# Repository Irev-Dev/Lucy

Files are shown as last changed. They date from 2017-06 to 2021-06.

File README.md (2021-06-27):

### Notice
Not maintained! Here's the back story. I started this project as way to mix a currenty hobby of racing quads and my new found love of OpenSCAD. As part of developing it I ran into frustrations with not being able to easly add fillets in OpenSCAD and so developed the [Round-Anything](https://github.com/Irev-Dev/Round-Anything) library to support this project. Some life events resulted in putting the project down and it lost steam.

My original [landing page](https://lucy-quad.kurthutten.com/) for lucy is still up in a graveyard state. and the [teaser video can be found here](https://vimeo.com/238244710).

# Lucy
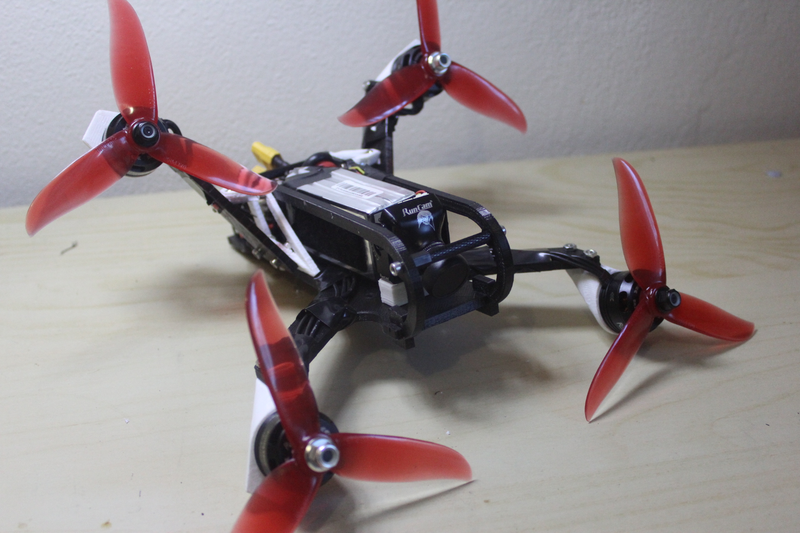
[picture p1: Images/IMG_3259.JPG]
 

OpenSCAD/Parametric Miniquad Frame, designed with aggressively tilted body and with flat arms for minimal blockage of the thrust columns. The result is a quad that is most aerodynamic when flown at its most aggressive angle as opposed to most miniquad frames which become less aerodynamic the further forward they are tilted.

The frame is intended to be made from carbonfiber with some printed parts. It's currently being prototyped so contributions are welcome. The frame also has a [thingiverse](https://www.thingiverse.com/thing:2403189) page, though I prefer to colaborate on github.

## Contributing
I thought it was about time I got this code up on github, so I don't have any immediate ideas of ways to contribute. I need to do an initial tidy of the code and then maybe I'll put together a plan of improvements/features that can be done. But by all means contact me with ideas or make a change and make a pull request.

At this stage the frame has not been tested at all, I have quad components arriving soon, I plan on testing it by printing it completely out of PLA (because it's cheap). It will break the first time it's crashed without a doubt, but I think PLA should be rigid and strong enough while in flight. If the frame progresses nicely and I get some carbonfiber cut I'm not sure what filament should be used for the final printed parts. I have some taulman 910 nylon which I think is probably a good mix of tough and rigid, but perhaps PETG or TPU should be used?

## Features
### Parametric
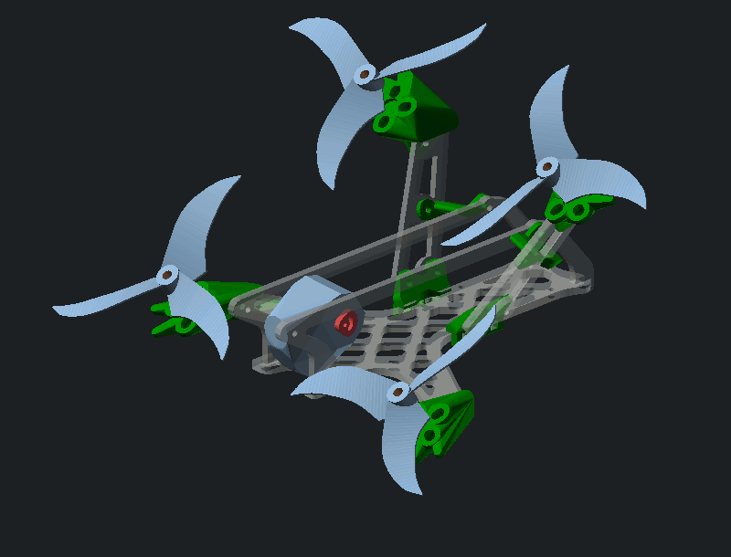
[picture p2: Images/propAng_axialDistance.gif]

Most dimensions can be tweaked. The image above for example shows the angle of the body relative to the props varying from 40 to 70 degrees and the distance between the rear props changing from 180 to 130mm.

### Low Drag
This is where I hope this frame will come into it's own. Most quad frames have a elongated body which creates negative lift while flying and creates more drag the more aggressively the quad is flown, while compact frames reduce this somewhat the arms of the quad still block a large amount of the thrust column which is inevitable when the motors are mounted directly to carbon fiber sheet. Lucy Kwad gets around this by having a very aggressively tilted body and tilted motor mounts. The body is tilted further than the camera angle so that during medium speed flight there is some drag but also some positive lift and in top speed flight the frame will be tilt so as to have the least drag. The arms of the quad are tilted at the same angle as the body thanks to the tilted motor mounts.
The image below shows the body tilt at a greater angle than the camera. 70 degrees in the images though this is a guess, testing is needed.

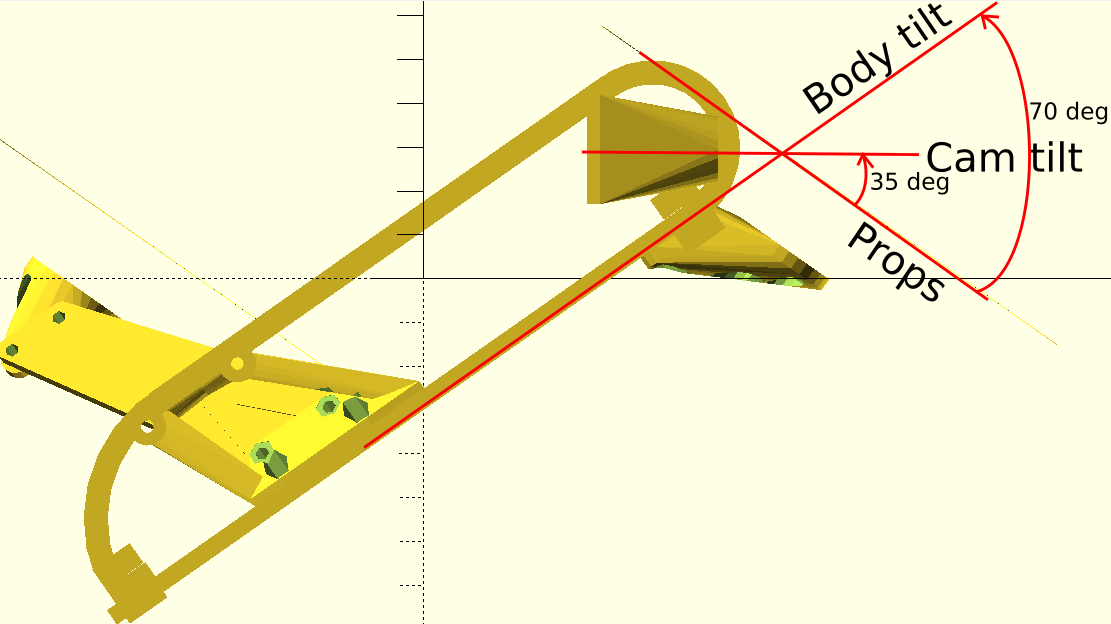
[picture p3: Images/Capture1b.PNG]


## Updates

26/06/2017 - Inital commit

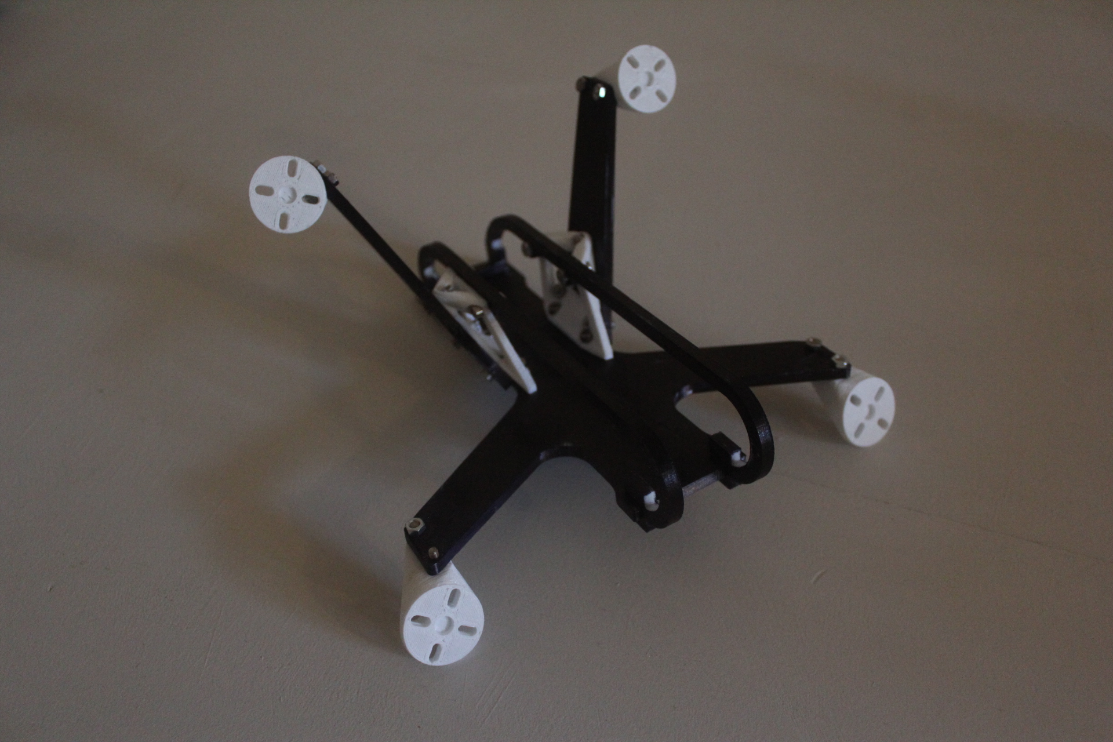
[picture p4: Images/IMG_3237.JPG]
 

28/06/2017 - I have spent the last two nights getting the code ready enough to print for the first (what I hope will be) flyable version. I got motivated when my motors arrived. I will print it out of PLA, it won't last long but hopefully I get an idea of how it will fly. 

30/06/2017 - I have done about 70% of the build for the first prototype. I'm getting excited. I had to put the props on just to see what it looks like, pretty happy with the aesthetics :)
The PLA is definitely worrisome. Because of the design of the quad the arms are still rigid enough in the direction of thrust bit I'm worried about the torque of the motors during fast spool ups. If it expodes when I punch it I just hope it doesn't damage any of the electronics. 

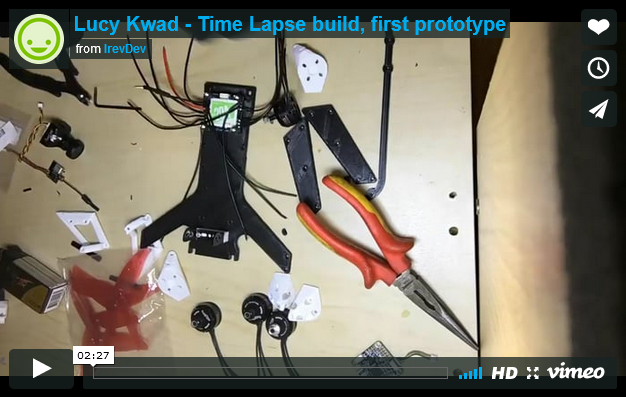
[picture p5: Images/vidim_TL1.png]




11/08/2017 - Got back to working on this and finish the electronics for the first prototype, ran into some interesting problems. With the default PID's as soon the quad armed it would start vibrating and would generate enough lift form trying to correct itself that it would start to take off. halving the PID values didn't fix it, and neither did quartering them. Then I tried re-enforcing the arms quickly with some balsa wood (as shown below) and now it seems to fly well with halved default PID values. This is the problem with using PLA, I won't be able to tune it properly and therefore see how it will actually fly until I bite the bullet and get it made in carbon fiber. It's been interesting trying to get it to fly though.

I have only done line of sight hovering so far, I hope to take it for a good FPV flight soon.

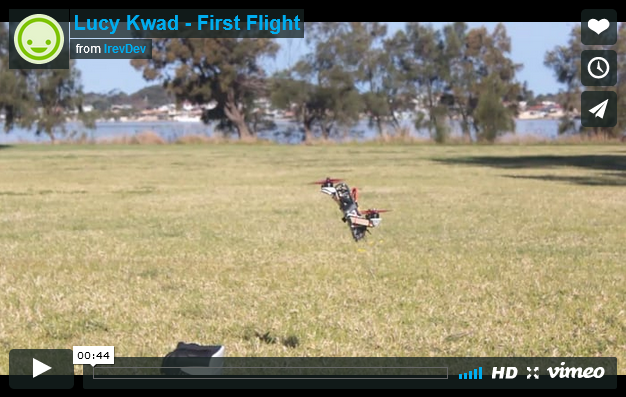
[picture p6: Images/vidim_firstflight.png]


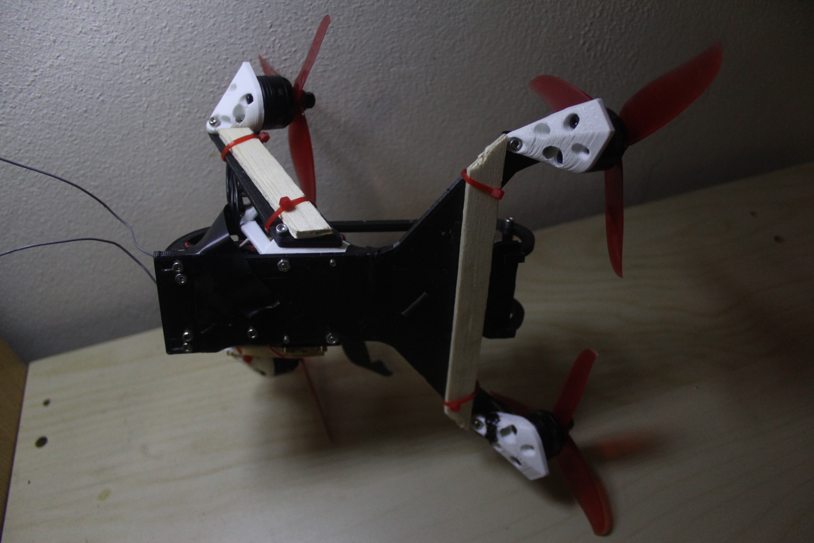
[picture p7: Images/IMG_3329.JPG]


15/08/2017 - A large update to the Lucy code just got merged into the master project on github. The change centers around the heavy use of the [polyRound()](https://github.com/Irev-Dev/Round-Anything) function instead of relying on primitives so much. Snap shot of the work in progress below.

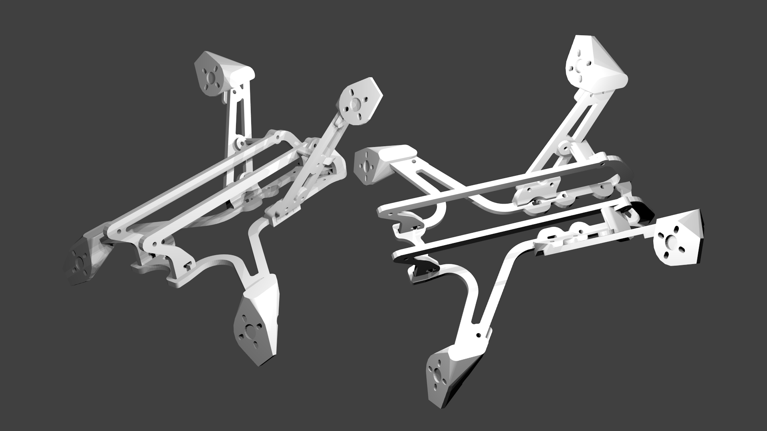
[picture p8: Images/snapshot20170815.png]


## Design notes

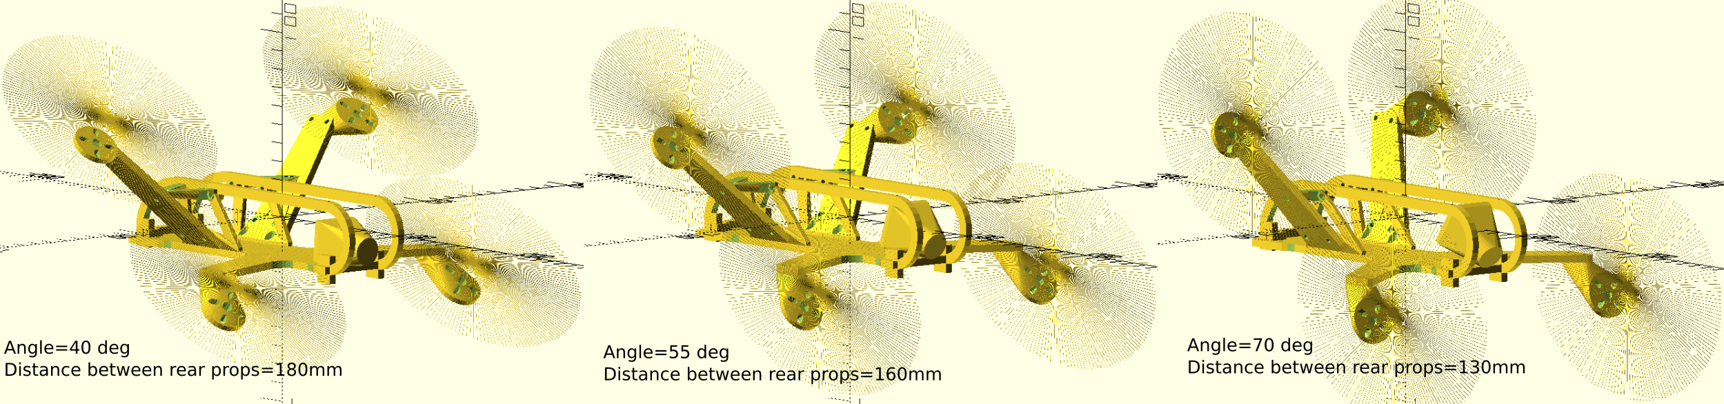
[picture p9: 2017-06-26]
Images/Capture11.png

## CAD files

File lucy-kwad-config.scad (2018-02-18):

/* 
Intellectual property is bullshit, steal this code

This code is licensed under GLPv3, which gives you permission to edit this code to meet your own purposes. 
However the idea that you need permission to edit and hack the things around you is insidious, 
and has been promoted by those who do not have your interests in mind. 
Intellectual property is bullshit.
*/

//include the modules 
include <lucy-kwad-modules.scad>
//include polyround tool 
include <libraries/polyround/polyround.scad>


//echo($vpr);echo($vpt);echo($vpd);//rotation, translation, camdist? focal?
//$vpr=[69.7, 0, 51.6];$vpt= [-1.03859, 2.44642, 3.51505];$vpd=412;//comment to stop the view from resetting each time

//VARIABLES//
PropD=5*25.4;//propsize inch
$fn=20;
gfn=6;
mot_s = [PropD+8,PropD+40,110,PropD+10]; //[x,yforLowMots,Z,YforUpMots]
dem=max(mot_s[0],mot_s[1],mot_s[3]);

theta = 70;
motP_MT = 3;//material thickness
motP_MT2=3;
motP_mntS=[15.8/2,19.2/2,15.8/2,19.2/2];//mount hole spacing [radA1,radA2,radB1,radB2]
motP_mntD = 3.2;//mounting hole diametr
motP_HD=6.5;//hex diameter
motP_HoS=6;//hex or square (hex=6,square=4);
motP_WMHCS=1.5;//Wing mount hole, counter sink start
motP_dia = 28;
motP_CD=6; //counter dia
motP_CA=45;//counter angle
motP_BR=4;//brace radius
motP_MG=[1,7];//diameter,offset from motP diameter
//motP_WMD=3.2;//wing mount dia
//motP_WMFD=5.7;//fastener dia
//motP_WMFS=6;//fasterner shap (6=hex,4=square)
motP_WMHD=7;//bolt head dia
//motP_WMFDp=2;//fasterner depth
motP_CHD=2;
motP_CHdia=9.5;

//none of these are used, though I might later?
//mot_ht=12;
//mot_dia=22;
//prop_ht=8;
//prop_dia=5*25.4;

//UWB upper wing brace
//UWB_min=3;//minimum material thickness
//UWB_MT=[4,3]; //material thickness1
//UWB_fast=[3.2,5,5.5,3,6];//[dia,head dia,hex dia,hex depth,hexOrSquare]fastner options
//UWB_BMH=4;//BMH
//UpperWingBrace(MT1=UWB_MT1,MT2=UWB_MT2,Hdia=UWB_Hdia,WBMO=UWB_MO)
UWB_MT1=2;
UWB_MT2=3;
UWB_Hdia=3.2;
UWB_MO=[5,4];//[x,z]
//this will be used soon
UWB_minP=0.5;//min print thickness (support material)
UWB_HoS=6; //hex or square 4=square 6=hex

//fuselage and rails, FR=fuselage rails
fs=[185,30+9,43]; //length width height
fs_mir=1;//min internal radius (set by the size of your routing bit)
fs_mer=0.2;//min external radius
fs_sr=2;//standard radius
fs_wtr=2;//wing tip radius
fs_wbr=[12,20];//wing base radius, [front, rear]
fs_minT=4;//min thickness
fs_bhd=5.7;//bolt head dia
fs_bd=3.2;//bolt dia
fs_bhh=3;//bolt head height
fs_bmt=3;//bolt min thickness
fs_ph=4;//post height
fs_pt=4;//post thickness
fusehozoff=-20;
FR=[4,5,6,65,35]; //[carbon thickness,other thickness,trasition radius, front angle, rear angle]
CarRT=4;
CarBT=FR[0];
RCutT=5.5;

//frameRail
FR_SD=[5,5];//slot depth1,slot depth2
FR_tol=0.2;
FR_CaT=4;//carbon thickness
FR_CuT=7;//cut thickness
FR_MT=3;//min thickness
FR_RA=20;//rear angle
FR_OH=13;//front overhang
FR_MIR=1;//min internal radius
FR_SR=3;//standard radius
FR_R1=20;//radius 1
FR_R2=5;//radius 2
FR_R3=10;//radius 3
FR_BHD=7;//bolt head dia
FR_BD=3.2;//bolt dia
FR_BHH=3;//bolt head height

WB_RSD=5;//rail slot depth
WB_CaT=4;
WB_PW=4;//post width
WB_mir=1;
WB_XP=-56;//X position
WB_BNO=1.5;//bottom nut offset
WB_tol=0.2;

Stack_HS=30.5;
Stack_HD=3.2;
Stack_PcbW=38;

//rough model of runcam eagle
camL=33; //length
camH=26.5; // height
camW=27;//width
camD=17;//lens diameter
camPP=3;//pivit point
camA=[theta,10];//angle
camMH=25;//mount height
camP=[fs[0]/2-43,24];//placement, [X,Z]
camRR=18;//rear room (behind camera)
camHP=[2,7];
camST=0.55;//shell thickness
camMT=2;//min thickness
camBMD=3.2;//bottom mount diameter
camBMH=12;//bottom mount height

//rearfastening
rearF_nh=2.5;// nut height
rearF_nf=5.3;// nut flats (distance between flats)
rearF_ha=20;//hull angle
rearF_bd=3.2;//bolt diameter

//CALCULATIONS// and some varibles

mot_cords=[[(mot_s[0]*cos(theta)+mot_s[2]*sin(theta))/2,mot_s[1]/2,(-mot_s[0]*sin(theta)+mot_s[2]*cos(theta))/2],
[(-mot_s[0]*cos(theta)-mot_s[2]*sin(theta))/2,mot_s[3]/2,(mot_s[0]*sin(theta)-mot_s[2]*cos(theta))/2]];
carbW=[33,23,4,4]; //wing [base width, tip width, thickness,radius]
carbWmin=2; //wing min thickness
carbLWTO = [-5,-3,15]; //lower wing tip offset [x,y,z]
carbLWR=[10,20];//lower wing radius [front,rear]
carbLWP=[22,fs[1]/2,mot_cords[0][2]+carbLWTO[2]]; //lower wing placement [x,y,z]
carbUWP=[-28,(fs[1]+carbW[2]*0)/2,carbLWP[2]+CarBT/2+UWB_MO[1]*0]; //lower wing placement [x,y,z]
carbUWTO = [-5,-12,-5]; //lower wing tip offset [x,y,z]
FR_RHP=[-fs[0]/2+fusehozoff+FR_SD[0]-FR_CuT+fs[2]*tan(FR_RA)+11,fs[2]-FR_CuT/2];//Rear hole placement, todo hardnum curently offset from the corrner of the rail by an abitary amount, ideally the hole should be placed just behind the wing so that it is still accessible with a allan key

LWXang = atan((mot_cords[0][2]+carbLWTO[2]-carbLWP[2])/(mot_cords[0][1]+carbLWTO[1]-carbLWP[1]));
UWXang = atan((mot_cords[1][2]+carbUWTO[2]-carbUWP[2])/(mot_cords[1][1]+carbUWTO[1]-carbUWP[1]));

TeMT=3;//tether Min thickness

//Upper wing Y length
UWYlen=pointDist([carbUWP[1],carbUWP[2]],[mot_cords[1][1]+carbUWTO[1],mot_cords[1][2]+carbUWTO[2]]);
//Upper wing radii points

UW_FWO=3; //front wing offset
UWingRP=[
[carbUWP[0],							UW_FWO,		3],
[mot_cords[1][0]+carbUWTO[0],			UWYlen,		3],	
[mot_cords[1][0]+carbUWTO[0]-carbW[1],	UWYlen,		3],	
[carbUWP[0]-carbW[0],					0,			3],
[carbUWP[0]-carbW.x/2,					UW_FWO,		10]
];
UWRYang=getAngle(UWingRP[2],UWingRP[3]);
UWFYang=getAngle(UWingRP[1],UWingRP[0]);

UWing_MFBMY=UWingRP[1].y-14;//motor front bottom mount Y
UWing_MRBMY=UWingRP[2].y-5;//motor rear bottom mount Y
UWing_MFBMSY=UWingRP[1].y-5;//motor front bottom mount small Y
UWing_MFBMX=interpX([UWingRP[0].x,UWingRP[0].y],[UWingRP[1].x,UWingRP[1].y],UWing_MFBMY);//motor front bottom mount X
UWing_MRBMX=interpX([UWingRP[3].x,UWingRP[3].y],[UWingRP[2].x,UWingRP[2].y],UWing_MRBMY);//motor rear bottom mount X
UWing_MFBMSX=interpX([UWingRP[0].x,UWingRP[0].y],[UWingRP[1].x,UWingRP[1].y],UWing_MFBMSY);//motor front bottom mount small X
UWing_XMHO=-carbWmin*3/cos(90-getAngle(UWingRP[0],UWingRP[1]));//X mount hole offset

UWing_BTO=11;
//UWing_MMH=round3points([UWing_MMP(4),[UWing_MMP(1)[0],UWing_MMP(1)[1],motP_mntD/2],UWing_MMP(2)])[2]+[UWing_XMHO,0];//motor mount hole
UWing_MMH=round3points([UWing_MMP(3),[UWing_MMP(0)[0],UWing_MMP(0)[1],(motP_mntD+motP_MT)/2],UWing_MMP(1)])[2]+[UWing_XMHO*0,0];//motor mount hole
UWing_FWMH=round3points([UWingRP[3],[UWingRP[0].x,UWingRP[0].y,5],UWingRP[1]])[2];//front wing mount hole
UWing_RWMH=round3points([UWingRP[2],[UWingRP[3].x,UWingRP[3].y,5],UWingRP[0]])[2];//rear wing mount hole
UWing_TMHY=(fs[2]/*-(carbUWP[2]-carbLWP[2])*/-UWB_MO[1]-FR_CuT)/sin(UWXang)-10;//Tether Mount Hole Y
//UWing_TMHY=(+fs[2]+carbUWP[2]-FR_CuT/2)/cos(UWXang);//Tether Mount Hole Y
TePoint=[100,fs.y/2,(carbLWP.z+fs.z/*-(carbUWP[2]-carbLWP[2])*/-FR_CuT*1.5)];//tether point - bad name will do for now.
//TePoint2=[100,carbUWP.y+(fs[2]/*-(carbUWP[2]-carbLWP[2])*/-UWB_MO[1]-FR_CuT)*cos(UWXang)+(carbW[2]/2+TeMT)*cos(UWXang)+TeMT*sin(UWXang),(carbLWP.z+fs.z/*-(carbUWP[2]-carbLWP[2])*/-FR_CuT*1.5-FR_CuT*cos(UWXang))];//tether point - bad name will do for now.
TePoint2=[-0,carbUWP.y,carbUWP.z]+[0,(UWing_TMHY-FR_CuT/sin(UWXang))*cos(UWXang)+(carbW[2]/2+TeMT)/sin(UWXang),(UWing_TMHY-FR_CuT/sin(UWXang))*sin(UWXang)];//(fs[2]-UWB_MO[1]-FR_CuT)/sin(UWXang)-FR_CuT*0-FR_CuT*sin(UWXang)];//tether point - bad name will do for now.
//#translate(TePoint)sphere(0.2);
//#translate(TePoint2)sphere(0.2);//translate([0,-10,0.2])cube([1,20,1]);
//UWing_TMHY=(fs[2]/*-(carbUWP[2]-carbLWP[2])*/-UWB_MO[1]-FR_CuT)/sin(UWXang);//Tether Mount Hole Y
UWing_TMHX=interpX([UWingRP[3].x,UWingRP[3].y],[UWingRP[2].x,UWingRP[2].y],UWing_TMHY)+9;//Tether Mount Hole X

UWing_BFT=[interpX([UWingRP[0].x,UWingRP[0].y],[UWingRP[1].x,UWingRP[1].y],UWingRP[0].y+UWing_BTO),UWingRP[0].y+UWing_BTO];//brace front top Y
UWing_BRT=[interpX([UWingRP[3].x,UWingRP[3].y],[UWingRP[2].x,UWingRP[2].y],UWingRP[3].y+UWing_BTO),UWingRP[3].y+UWing_BTO];//brace rear top Y
UWing_BFB=[interpX([UWingRP[0].x,UWingRP[0].y],[UWingRP[1].x,UWingRP[1].y],UWingRP[0].y-20),UWingRP[0].y-20];//brace front bottom Y
UWing_BRB=[interpX([UWingRP[3].x,UWingRP[3].y],[UWingRP[2].x,UWingRP[2].y],UWingRP[3].y-20),UWingRP[3].y-12];//brace rear bottom Y


l=fs[0];
w=fs[1];

fs_BPC=carbUWP[0]-carbW[0]/2;//bolt point centre

LWing_MFBMY=LWingRP(2).y-5;//motor front base mount Y
LWing_MRBMY=LWingRP(1).y-14;//motor rear base mount Y
//LWing_MFBMSY=LWingRP(2).y-3;//motor front base mount SMALL Y
LWing_MRBMSY=LWingRP(1).y-5;//motor front base mount SMALL Y
LWing_MFBMX=interpX([LWingRP(3).x,LWingRP(3).y],[LWingRP(2).x,LWingRP(2).y],LWing_MFBMY);//motor front bottom mount X
LWing_MRBMX=interpX([LWingRP(0).x,LWingRP(0).y],[LWingRP(1).x,LWingRP(1).y],LWing_MRBMY);//motor rear bottom mount X
LWing_MRBMSX=interpX([LWingRP(0).x,LWingRP(0).y],[LWingRP(1).x,LWingRP(1).y],LWing_MRBMSY);//motor front bottom mount Small X
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

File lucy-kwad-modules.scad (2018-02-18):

module WbraceP(partLayout = 0){
	difference(){
		hull(){
			translate([carbUWP.x - 8, fs.y / 2 - 4 + 1.6, carbUWP.z])cylinder(h = 4, d = 6);
			translate([carbUWP.x - 8 - 5, fs.y / 2, carbLWP.z])cube([10, 4, 4]);
			tranX(carbUWP.x - 8)UpperWingSpace()tranY(UW_FWO + 3.5)cylinder(h = 4, d = 6);

		}
		translate([carbUWP.x - 8, fs.y / 2 - 4 + 1.6, carbUWP.z])cylinder(h = 4, d = 4);
		tranX(carbUWP.x - 8)UpperWingSpace()tranY(UW_FWO + 3.5)cylinder(h = 4, d = 4);
		wingU3(100, 0.2);
		fuse3(100, 0.2);
	}
}
{module WbraceC(partLayout = 0)
	tranX(-100 * partLayout){//wing brace carbon fiber
		neg = partLayout == 0 ? 1 : 0;
		braceH = fs.z - CarBT - FR_CuT + WB_RSD;
		echo(braceH);
		//moveRadiiPoints(rp,tran=[0,0],rot=0)
		braceP = concat(//brace points
			[[carbUWP.z, 0, 0]],
			moveRadiiPoints(WB_PP(), [carbUWP.z, fs.y / 2 - WB_BNO - (fs_bd + fs_bhd) / 2]),
			moveRadiiPoints(fs_BP(), [carbUWP.z, fs.y / 2 - WB_BNO - fs_bd / 2], 90),
			[[carbUWP.z, carbUWP.y, 0]],
			let(h = 3 + WB_PW)moveRadiiPoints(WB_PP(), [carbUWP.z + h, carbUWP.y + (h) / tan(UWXang)], -UWXang),
			moveRadiiPoints(fs_BP(), [carbUWP.z + braceH / 2.5, carbUWP.y + braceH / 2.5 / tan(UWXang)], 90 - UWXang),
			moveRadiiPoints(WB_PP(), [carbUWP.z + braceH - 11, carbUWP.y + (braceH - 11) / tan(UWXang)], -UWXang),
			//[[carbUWP.z+braceH,carbUWP.y+braceH/tan(UWXang),0]],
			[[carbUWP.z + braceH - 7, (fs.y / 2 + carbUWP.y + (braceH - 6) / tan(UWXang)) / 2 - 3, 10]],
			[[carbUWP.z + braceH, fs.y / 2, 0]],
			[[carbUWP.z + braceH - WB_RSD, fs.y / 2, 0]],
			[[carbUWP.z + braceH - WB_RSD, fs.y / 2 - FR_CaT, 0]],
			[[carbUWP.z + fs.z - CarBT, fs.y / 2 - FR_CaT, 0]],
			[[carbUWP.z + fs.z - CarBT + 2, 0, 70]]
		);
		color("red")tranX(WB_XP)rotate([0, -90 * neg, 0])linear_extrude(WB_CaT)shell2d(-4, 0, 1)difference(){
			polygon(polyRound(mirrorPoints(braceP, atten = [1, 1]), gfn));
			for (i = [0, 1])mirror([0, i, 0]){
				translate([carbUWP.z + braceH - WB_RSD, fs.y / 2 - FR_CaT - WB_tol / 2, 0])internalSq([FR_CuT * 3, FR_CaT + WB_tol], WB_mir);
				//#translate([carbUWP.z+braceH-14,carbUWP.y+(braceH-14)/tan(UWXang)])circle(WB_mir);
				for (i = [1, 4, 15, 18, 28])translate(parallelFollow([braceP[i - 1], braceP[i], braceP[i + 1]], thick = WB_mir * cos(45), minR = 0))circle(WB_mir);
				//translate(parallelFollow([braceP[14],braceP[15],braceP[16]],thick=WB_mir*cos(45),minR=0))circle(WB_mir);
				//translate(parallelFollow([braceP[17],braceP[18],braceP[19]],thick=WB_mir*cos(45),minR=0))circle(WB_mir);
				//translate(parallelFollow([braceP[27],braceP[28],braceP[29]],thick=WB_mir*cos(45),minR=0))circle(WB_mir);
			}
		}
	}
	function WB_PP(index1, index2)=//post points
	let(WB_PP = [//post points
		[0, -WB_PW, WB_mir],
		[-WB_CaT, -WB_PW, 0],
		[-WB_CaT, 0, 0],
		[0, 0, WB_mir],
	])
	range(WB_PP, index1, index2);
}
module thecam(index = 0){
	//translate([72,0,cos(theta-camA)*(camD/2)+carbLWP[2]+CarBT/2])rotate([0,theta-camA,0])difference(){
	if (index == 0) {
		translate([64 + fusehozoff, 0, carbLWP[2] + CarBT / 2 + camMH])difference(){
			union(){
				//bracket
				translate([-camM[0] / 2, camM[1] / 2 - camM[3], -camM[4]])cube([camM[0], camM[3], camM[2]]);
				translate([-camM[0] / 2, 0, -camM[4]])cube([camM[0], camM[1] / 2, camM[3]]);
				rotate([0, theta - camA, 0])hull(){//camera unit
					translate([-camPP, -camW / 2, -camH / 2])cube([10, camW, camH]);
					translate([camL - camPP, 0, 0])rotate([0, 90, 0])cylinder(d = camD, h = 0.01);

				}
			}
			union(){
				translate([0, camM[6] / 2, -50])cylinder(d = camM[5], h = 40);

			}
		}
	} else {
		translate([54 + fusehozoff, 0, carbLWP[2] + CarBT / 2 + camMH])translate([0, camM[6] / 2, -50])cylinder(d = camM[5], h = 40);

	}
}
module cam(expand = 0, mode = 0){
	div = mode == 0 ? 2 : 10;
	sl = 10;//square length
	dia = 17;
	translate([camP[0], 0, carbLWP[2] + camP[1]]){
		hull()for(i = [70 - camA.x, 70 - camA.y])rotate([0, i, 0])if(expand > 0) translate([camL + sl * 2 - camHP[1] + expand, 0, 0])rotate([0, -90, 0])cylinder(h = camL + sl - camHP[1] + expand, d = dia + expand * 2);
		if (mode == 0) {
			//hull()rotate([0, 20, 0])difference(){
			hull()for(i = [70 - camA.x:(camA.x - camA.y) / div:70 - camA.y])rotate([0, i, 0])difference(){
				union(){
					translate([sl / 2 - camHP[1] - expand, 0, 0])cube([sl, camW + expand * 2, camH + expand * 2], true);
					translate([camL - camHP[1] + 2 + expand, 0, 0])rotate([0, -90, 0])cylinder(h = 3, d = dia + expand * 2);
				}
				union(){
					translate([0, w / 2 - 3, 0])rotate([-90, 0, 0]){
						cylinder(d = 3.2, h = 10);
						translate([camHP[0] - camHP[1], 0, 0])cylinder(d = 3.2, h = 10);
					}
				}
			}
		} else {
			for (i = [70 - camA.x:(camA.x - camA.y) / div:70 - camA.y])hull(){
				rotate([0, i, 0])translate([camL + sl / 2 - camHP[1] + expand, 0, 0])rotate([0, -90, 0])cylinder(h = 3, d = dia + expand * 2);
				rotate([0, i + 1, 0])translate([camL + sl / 2 - camHP[1] + expand, 0, 0])rotate([0, -90, 0])cylinder(h = 3, d = dia + expand * 2);
			}
		}
	}
}
module camRef(partLayout = 0){
	mntT = 3;//mount thick
	cen = [camP.x, carbLWP.z + camP.y];
	H = (camHP.y - camHP.x);//hypotenuse
	p1a = [-cos(theta - camA.x - 10) * H, sin(theta - camA.x - 10) * H] + cen;
	p2a = [-cos(theta - camA.y + 10) * H, sin(theta - camA.y + 10) * H] + cen;
	p1b = [-cos(theta - camA.x - 10) * H - 0.01, sin(theta - camA.x - 10) * H - 0.01] + cen;
	p2b = [-cos(theta - camA.y + 10) * H - 0.01, sin(theta - camA.y + 10) * H - 0.01] + cen;
	thinwall_1side = concat(
		[[camP.x - camRR, 0, 1]],
		[[camP.x - camRR, railTE(0).y, 10]],
		railTE(1, 2),
		[[frontRailClip(1).x, frontRailClip(1).y, 0]]
	);

	thinwall = concat(
		thinwall_1side,
		//RailCustomiser(thinwall_1side,camST,0.5,1,1,0,0)
		//RailCustomiser(rp,thick,minR,sgn=1,endpointenable=1,endAng1=0,endAng2=0)
		revList(RailCustomiser(thinwall_1side, o1 = camST + 0.06/*camMT*1.3*/, minR = 0.5, mode = 0))
	);
	thinwall1 = concat(
		thinwall_1side,
		//RailCustomiser(thinwall_1side,camMT*1.3,0.5,1,1,0,0)
		revList(RailCustomiser(thinwall_1side, o1 = camMT * 1.3, minR = 0.5, mode = 0))
	);
	//#for(i=thinwall_1side)rotate([-90,0,0])translate(i)circle(1);
	//	#for(i=thinwall)rotate([-90,0,0])translate(i)circle(0.5);
	//	#for(i=thinwall1)rotate([-90,0,0])translate(i)circle(1);
	//	echo(len(thinwall),len(thinwall1));
	railsubtract = concat(
		//railTE(),
		//[[frontRailClip(0).x,-50,0]],
		//RailCustomiser(concat([rearRailClip(7)],railTE()),30,2,1,0)
		RailCustomiser(concat(railTE(), [[frontRailClip(0).x, -50, 0]]), o1 = 0, o2 = 60, minR = 2, mode = 0, a2 = -1)
	);
	bottomMountS = [//bottomMountSubtract points
		[camST, camBMH, 3],
		[camMT * 2 + camBMD, camBMH - camMT * 2 - camBMD + camST, 3],
		[camMT * 2 + camBMD, camBMH - camMT * 2 - camBMD + camST - 20, 0],
		[camMT * 2 + camBMD + 4, camBMH - camMT * 2 - camBMD + camST - 20, 0],
		[camMT * 2 + camBMD + 4, camBMH + 4, 0],
		[camST, camBMH + 4, 0],
	];
	tranX(60 * partLayout)rotX(partLayout * 180)difference(){
		union(){
			CamMSpace(0)difference(){
				// linear_extrude(camBMH + 2)round2d(0, 2){
				// 	tranX(camMT + camBMD / 2)circle(d = camMT * 2 + camBMD);
				// 	square([camST, fs.y / 4]);
				// }
				// tranY(fs.y / 4)rotX(90)linear_extrude(fs.y / 2)polygon(polyRound(bottomMountS, gfn, 0));
			}
			hull(){
				// intersection(){
				// 	tranY(fs.y / 2 - carbW[2])rotX(90)linear_extrude(mntT * 3)translate([fs.x / 2 + fusehozoff + FR_OH + FR_CuT * tan(atan(fs.z / 2 / FR_OH) / 2 + 90), (carbLWP[2] - carbW[2] / 2) + fs.z - FR_CuT])circle(d = FR_BD + mntT * 3);
				// 	translate([0, w / 2 - FR_CaT, carbLWP[2] - carbW[2] / 2])rotate([90, 0, 0])linear_extrude(camMT * 3)polygon(polyRound(thinwall1, gfn, 0));
				// }
				// tranY(fs.y / 2 - carbW[2])rotX(90)linear_extrude(mntT * 3)translate([fs.x / 2 + fusehozoff + FR_OH + FR_CuT * tan(atan(fs.z / 2 / FR_OH) / 2 + 90), (carbLWP[2] - carbW[2] / 2) + fs.z - FR_CuT])circle(d = FR_BD + mntT * 2);
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

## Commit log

2017-06-28 first protype
    Still rough around the edges, but I'm going to print this version entirely in PLA, it won't last long but I should be able to get some idea of how it flys.
    [Lucy_Kwad.scad]
2017-08-18 mmix
    -An attempt and custom mmix for this frame (doesn't account for weight distribution for pitch)
    [lucy-kwad-config.scad]
2017-08-18 Props & comments
    -Nicer looking props (thrown together, just for aesthetics, not to be printed)
    -Comments and neating.
    [lucy-kwad-modules.scad]
2018-02-18 merging changes made locally since last time the git was updated, to be merged
    [lucy-kwad-config.scad, lucy-kwad-modules.scad]
2018-02-18 add polyround library as submodule and update include<> reference to suit
    [lucy-kwad-config.scad]
